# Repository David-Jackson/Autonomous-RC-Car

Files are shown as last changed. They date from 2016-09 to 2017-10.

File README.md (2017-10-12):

# Autonomous RC Car
###### David Jackson - Summer 2016

## Objective

Develop an autonomous remote-controlled (RC) car using an Arduino and PID controllers.

## Introduction

The idea of developing an autonomous RC car was brought up by [Dr. Peters](http://dianelpeters.com/) and initially developed by Dwarkesh Iyengar in October of 2015 [(link)](http://dianelpeters.com/DSCC_2015_Development_of_a_Miniaturized_Autonomous_Vehicle.pdf). Iyengar used a microcontroller unit to control the car. The microcontroller would receive commands and transmit data to a myRIO controller unit using Xbee radio transmitters. Building on Iyengar’s work, the goal of this project was to place the controller in the RC car, removing the dependency on the myRIO controller and making the car fully autonomous.

## Iterations

This project went through three design iterations during the author’s term.

### Iteration 1: Servo Mounted LIDAR

The first design iteration centered around using one LIDAR sensor  mounted to a servo motor to measure the distance to the vehicle’s surroundings. The servo motor would rotate 90 degrees, obtaining a distance reading at every degree interval. Wiring for the Lidar/Servo assembly and the Arduino can be seen in [Figure 1](#fig-1). This concept was first tested by placing the LIDAR/Servo assembly in 12 inches away from a wall. The servo motor looped through 45 and 135 degrees and back with different delay times between degrees ranging from 5 and 50 milliseconds. This was repeated 10 times for data validation. 

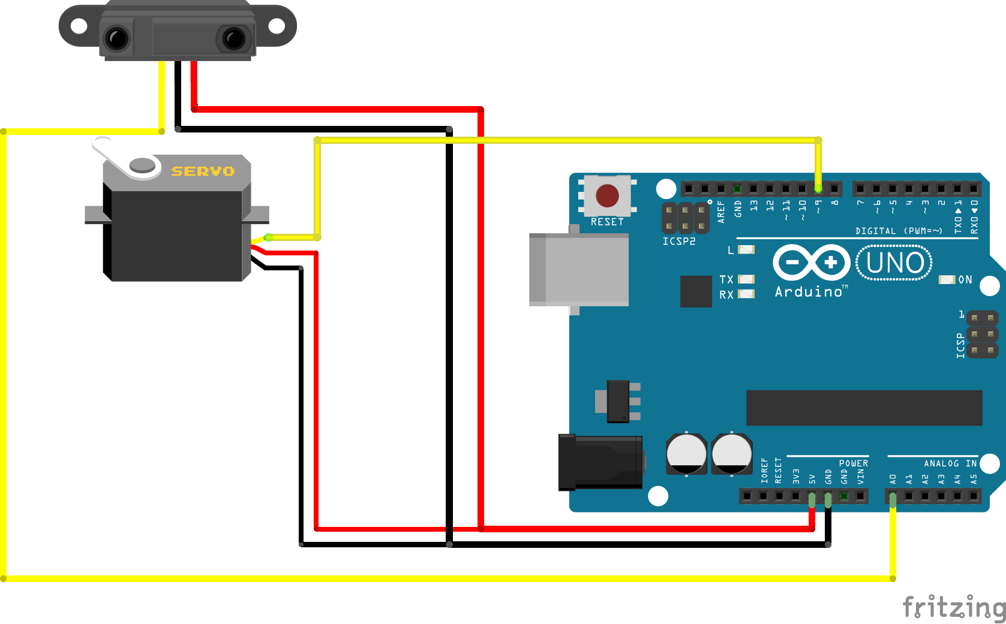
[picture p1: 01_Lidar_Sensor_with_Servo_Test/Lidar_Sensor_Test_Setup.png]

Figure 1: LIDAR/Servo Wiring Schematic

The results of the LIDAR/Servo test showed a deviation of around 10 cm between measurements at all speeds tested. This result was not within the accuracy needed for this project. A closer look into the specification sheet for the sensor showed a range between 0 and 40 meters and an accuracy of 0.025 meters. The LIDAR sensor was meant for larger-scale use where the difference between centimeters was not as important. IR distance sensors were implemented as an alternative to LIDAR, which is described in Iteration 3.

### Iteration 2: Radio Transmission Data Collection

In an attempt to collect real-time analytics from the RC car without the need of a wire, two radio transmitters  where considered. Wiring schematic for this iteration can be seen in [Figure 2](#fig-2). An Arduino Nano was used as the controller. The controller was connected to an accelerometer/gyroscope/ magnetometer board  for acceleration readings and the steering potentiometer for steering direction readings. Additionally, the controller was connected to a bi-directional motor controller IC, also called a H-bridge to control the speed and direction of the steering and drive motors (in Iteration 3 this was replaced with the Adafruit Motor Shield, which is based on a similar chip). Finally, he controller was then connected to the radio transmitter, which would send acceleration, steering direction, and motor speed data to the radio receiver, seen in [Figure 3](#fig-3), which would then be able to be seen on a computer. 

During testing, the Arduino controller took approximately 1.5 seconds to collect and send the data to the radio receiver. This delay was most likely due to the lack of processing power on the Arduino and could be avoided with a more powerful controller. This large of a delay in sensor data acquisition would be detrimental to the performance of the controller, so the concept of relaying data using radio was tabled and another iteration was developed.

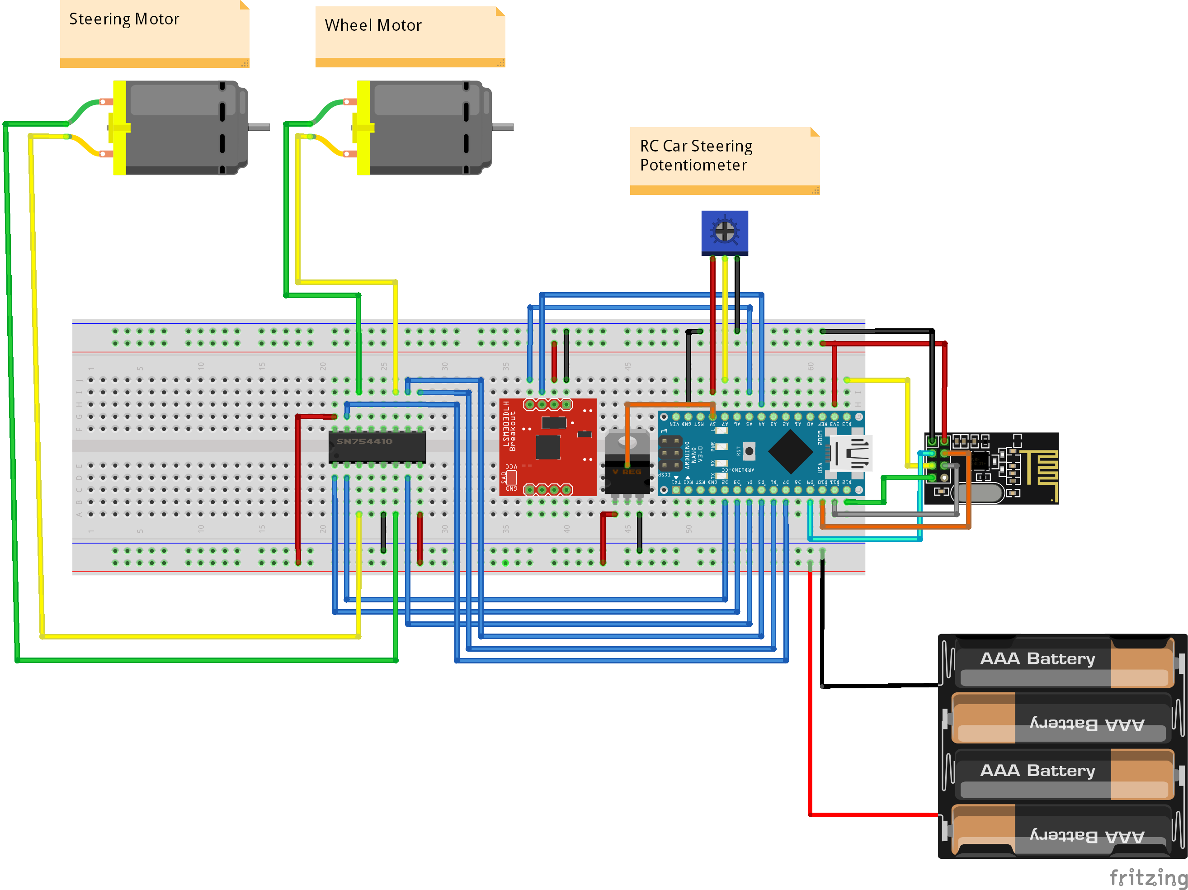
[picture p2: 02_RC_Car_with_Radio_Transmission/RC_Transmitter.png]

Figure 2: Radio Transmitter Controller Wiring Schematic

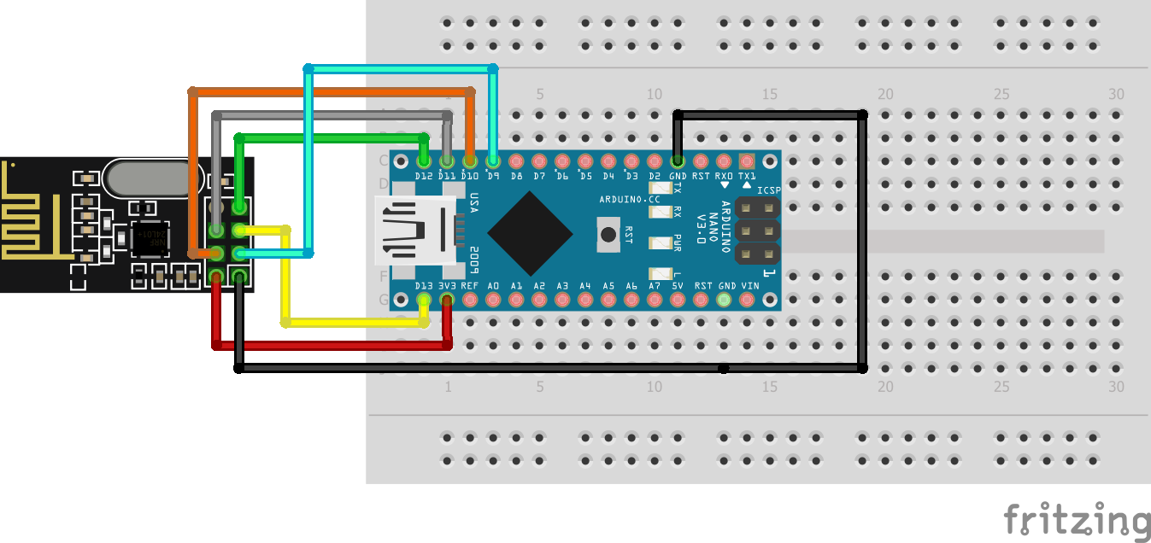
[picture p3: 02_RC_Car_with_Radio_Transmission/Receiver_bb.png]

Figure 3: Radio Receiver Module

### Iteration 3: RC Car with IR Distance Sensors

The final design of the autonomous RC car consisted of three [IR distance sensors](https://www.amazon.com/GP2Y0A21YK0F-Sharp-Distance-10-80cm-Compatible/dp/B00IMOSEJA), an Arduino, and two PID controllers. The wiring schematic for this design can be found in [Figure 4](#fig-4). This iteration was completely self-sufficient and did not require any radio transmission or outside control. Adapted from Microsoft’s Internet of Things [Github repository](https://github.com/ms-iot/wod-autorc)  on an autonomous RC car, the vehicle would determine its surroundings using the IR sensors and decide whether to turn, stop, or continue straight. 

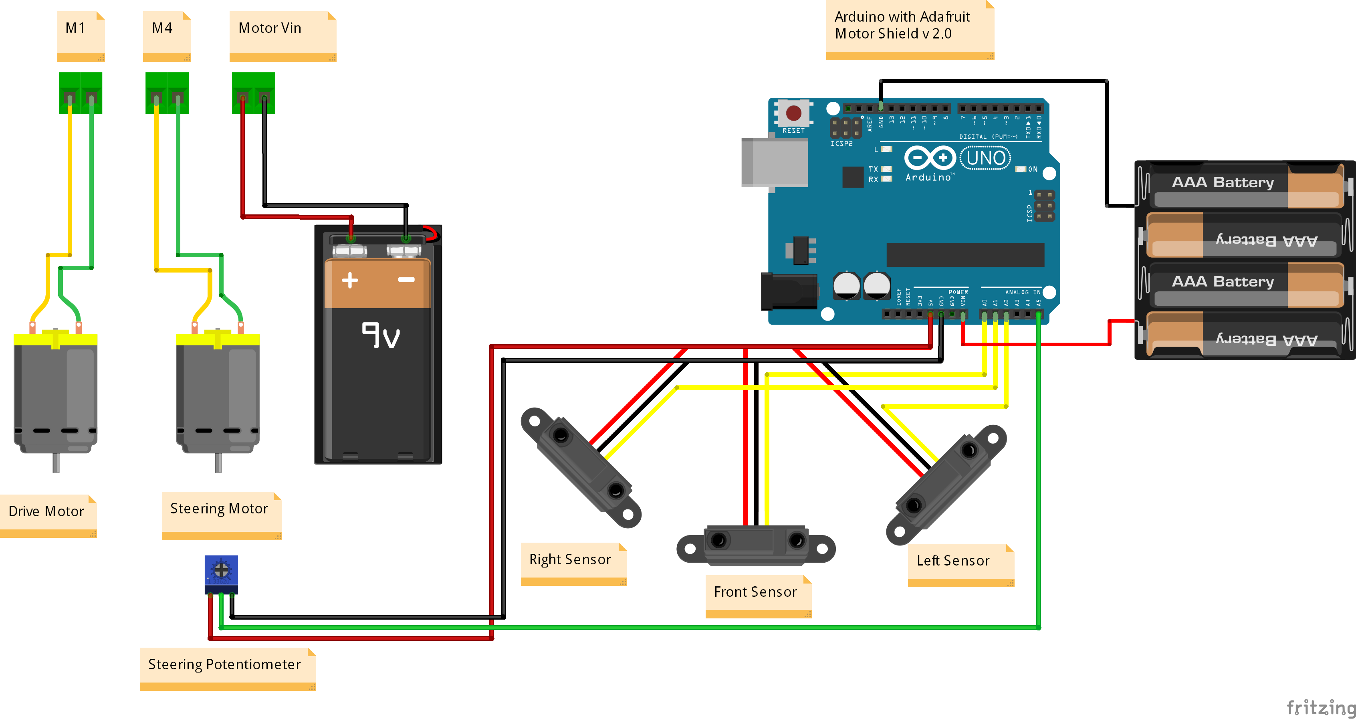
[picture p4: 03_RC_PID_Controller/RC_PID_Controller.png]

Figure 4: RC Car with IR Distance Sensors Wiring Diagram 

This design was similar to the radio transmitter iteration, except with an Arduino Uno instead of an Arduino Nano, an Adafruit Motor Shield v2.0 instead of the H-bridge Motor Driver IC, and with the addition of three IR distance sensors mounted to the front of the vehicle to measure direction straight ahead, to the right of the vehicle, and to the left of the vehicle. M1, M4, and Motor Vin seen in [Figure 4](#fig-4) represent the terminal blocks on the motor shield. It is also important to notice that the Arduino and motors are being powered by two different power sources to eliminate sensor noise produced by the motors’ energy consumption. 

#### Arduino PID Code

Below is all the code relating to the Arduino PID controller library. For a complete code file, see the code in the [project folder](/03_RC_PID_Controller/Arduino Code/IS_controller_2/IS_controller_2.ino).

Include the Arduino PID Library.
```c++
#include<PID_v1.h>
```

Next, define the variables used for the Drive PID Controller.
```c++
float Kp_drive = 0.8;  // Proportional Gain
float Ki_drive = 0.07; // Integral Gain
float Kd_drive = 0.12; // Derivative Gain
double Setpoint_drive, Input_drive, Output_drive;                                       
```

Initilize the Drive PID Controller.
```c++
PID drivePID(&Input_drive, &Output_drive, &Setpoint_drive, Kp_drive, Ki_drive, Kd_drive, DIRECT);
```

Define Variables for the Steering PID Controller.
```c++
float Kp_steer = 0.8;
float Ki_steer = 0.07;
float Kd_steer = 0.12; 
double Setpoint_steer, Input_steer, Output_steer;                                       
```

Initilize the Steering PID Controller.
```c++
PID steerPID(&Input_steer, &Output_steer, &Setpoint_steer, Kp_steer, Ki_steer, Kd_steer, DIRECT);
```

In the setup() function, set the Drive PID setpoint, the PID mode, and the output limits. In this case the output is going to be the speed of the motor, which we want to be between -50 (reverse) and 50 (forward). NOTE: the maximum motor speed is -255 and 255. 
```c++
Input_drive = readPosition();
Setpoint_drive = 300;
drivePID.SetMode(AUTOMATIC);
drivePID.SetOutputLimits(-50, 50);
```

Now do the same for the Steering PID controller, with the motor speed being limited to between -40 and 40.
```c++
Input_steer = readPosition();
Setpoint_steer = 650;
steerPID.SetMode(AUTOMATIC);
steerPID.SetOutputLimits(-40, 40);
```

In the loop() function, read angle of the steering wheels from the potentiometer, compute the PID response, and set the motor speed accordingly.
```c++
Input_steer = readSteering();
steerPID.Compute();
setSteerSpeed(Output_steer);
```

Read angle of the steering wheels from the middle IR distance sensor, compute the PID response, and set the motor speed accordingly. 
```c++
Setpoint_drive = 300;
Input_drive = readPosition();
drivePID.Compute();
if (stopped) {
  setDriveSpeed(0);
} else {
  setDriveSpeed(Output_drive);
}
```

## Conclusions

This independent study was able to design and create an autonomous RC car using an Arduino. The Arduino uses IR distance sensors to determine its surroundings and a potentiometer to determine the angle of the front wheels. The Arduino PID library was successfully implemented on the Arduino using two controllers: one for the control of the angle of the front wheels, and one for the speed of the driven rear wheels. 

In the continuation of this project, the author recommends fine tuning of the PID controllers and to add a data collection unit to the Arduino. The drive PID controller should be fine-tuned to an over damped controller to eliminate any overshoot when approaching an object. Additionally, fine-tuning the steering controller will also eliminate any steering overshoot and will guarantee the steering will reach steady-state. The addition of a data collection unit would be very beneficial to this project to analyze vehicle acceleration and sensor effectiveness. Data collection can be added to the Arduino using a [Data Logger shield](https://www.amazon.com/SD-Shield-for-Arduino-v4-0/dp/B00BPGPNH8) or even an [Ethernet Shield](https://www.amazon.com/Ethernet-Shield-Network-Expansion-Arduino/dp/B00AXVX5D0/), which both include the ability to read and write files to an SD card.

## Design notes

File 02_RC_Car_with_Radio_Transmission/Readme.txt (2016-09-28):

08/12/2016

The idea behind this design was to be able to transmit data wirelessly to a computer to analyse the RC Car's current state. This included the vehicle's acceleration, it's proximity to other objects, and the current motor speeds. However, due to the hardware limitations of the accelerometer and Arduino, the time in between transmissions averages 1.5 seconds. This large of a duration between transmissions would not yield usable data, so a different design was considered.

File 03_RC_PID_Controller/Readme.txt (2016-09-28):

09/07/2016

This design was inspired by Microsoft's Internet of Devices Github project. It involves infrared distance sensors and PID controllers to sense the vehicle's surroundings and make a decision on where to move next.

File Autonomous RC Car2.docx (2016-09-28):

# Autonomous RC Car

###### David Jackson - Summer 2016

## Objective

Develop an autonomous remote-controlled (RC) car using an Arduino and PID controllers.

## Introduction

The idea of developing an autonomous RC car was conceived by Dr. Peters and initially developed by Dwarkesh Iyengar in October of 2015 (link) (http://dianelpeters.com/DSCC_2015_Development_of_a_Miniaturized_Autonomous_Vehicle.pdf). Iyengar used a microcontroller unit to control the car. The microcontroller would receive commands and transmit data to a myRIO controller unit using Xbee radio transmitters. Building on Iyengar’s work, the goal of this project was to place the controller in the RC car, removing the dependency on the myRIO controller and making the car fully autonomous.

## Iterations

This project went through three design iterations during the author’s term.

### Iteration 1: Servo Mounted LIDAR

The first design iteration centered around using one LIDAR sensor mounted to a servo motor to measure the distance to the vehicle’s surroundings. The servo motor would rotate 90 degrees, obtaining a distance reading at every degree interval. Wiring for the Lidar/Servo assembly and the Arduino can be seen in Figure 1. This concept was first tested by placing the LIDAR/Servo assembly in 12 inches away from a wall. The servo motor looped through 45 and 135 degrees and back with different delay times between degrees ranging from 5 and 50 milliseconds. This was repeated 10 times for data validation.

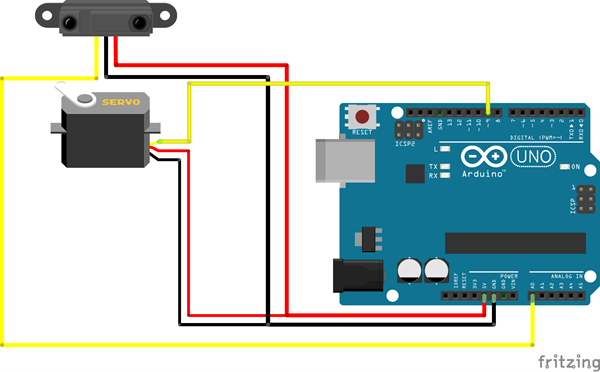
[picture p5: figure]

Figure 1: LIDAR/Servo Wiring Schematic

The results of the LIDAR/Servo test showed a deviation of around 10 cm between measurements at all speeds tested. This result was not within the accuracy needed for this project. A closer look into the specification sheet for the sensor showed a range between 0 and 40 meters and an accuracy of 0.025 meters. The LIDAR sensor was meant for larger-scale use where the difference between centimeters was not as important. IR distance sensors were implemented as an alternative to LIDAR, which is described in Iteration 3.

### Iteration 2: Radio Transmission Data Collection

In an attempt to collect real-time analytics from the RC car without the need of a wire, two radio transmitters where considered. Wiring schematic for this iteration can be seen in Figure 2 (https://jbt.github.io/markdown-editor/). An Arduino Nano was used as the controller. The controller was connected to an accelerometer/gyroscope/ magnetometer board for acceleration readings and the steering potentiometer for steering direction readings. Additionally, the controller was connected to a bi-directional motor controller IC, also called a H-bridge to control the speed and direction of the steering and drive motors (in Iteration 3 this was replaced with the Adafruit Motor Shield, which is based on a similar chip). Finally, he controller was then connected to the radio transmitter, which would send acceleration, steering direction, and motor speed data to the radio receiver, seen in Figure 3, which would then be able to be seen on a computer.

During testing, the Arduino controller took approximately 1.5 seconds to collect and send the data to the radio receiver. This delay was most likely due to the lack of processing power on the Arduino and could be avoided with a more powerful controller. This large of a delay in sensor data acquisition would be detrimental to the performance of the controller, so the concept of relaying data using radio was tabled and another iteration was developed.

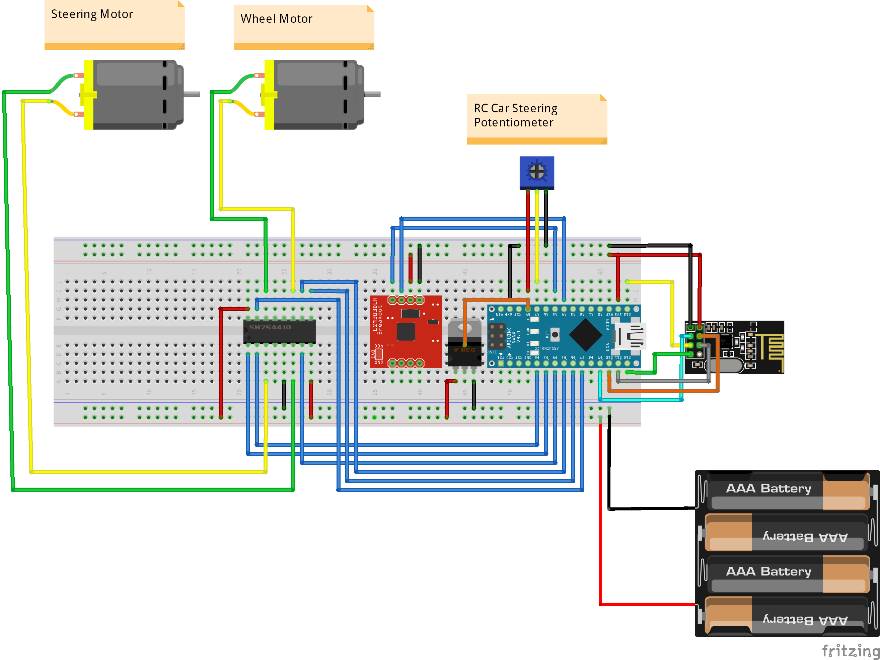
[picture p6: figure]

Figure 2: Radio Transmitter Controller Wiring Schematic


Figure 3: Radio Receiver Module

### Iteration 3: RC Car with IR Distance Sensors

The final design of the autonomous RC car consisted of three IR distance sensors (https://www.amazon.com/GP2Y0A21YK0F-Sharp-Distance-10-80cm-Compatible/dp/B00IMOSEJA), an Arduino, and two PID controllers. The wiring schematic for this design can be found in Figure 4. This iteration was completely self-sufficient and did not require any radio transmission or outside control. Adapted from Microsoft’s Internet of Things Github repository (https://github.com/ms-iot/wod-autorc) on an autonomous RC car, the vehicle would determine its surroundings using the IR sensors and decide whether to turn, stop, or continue straight.

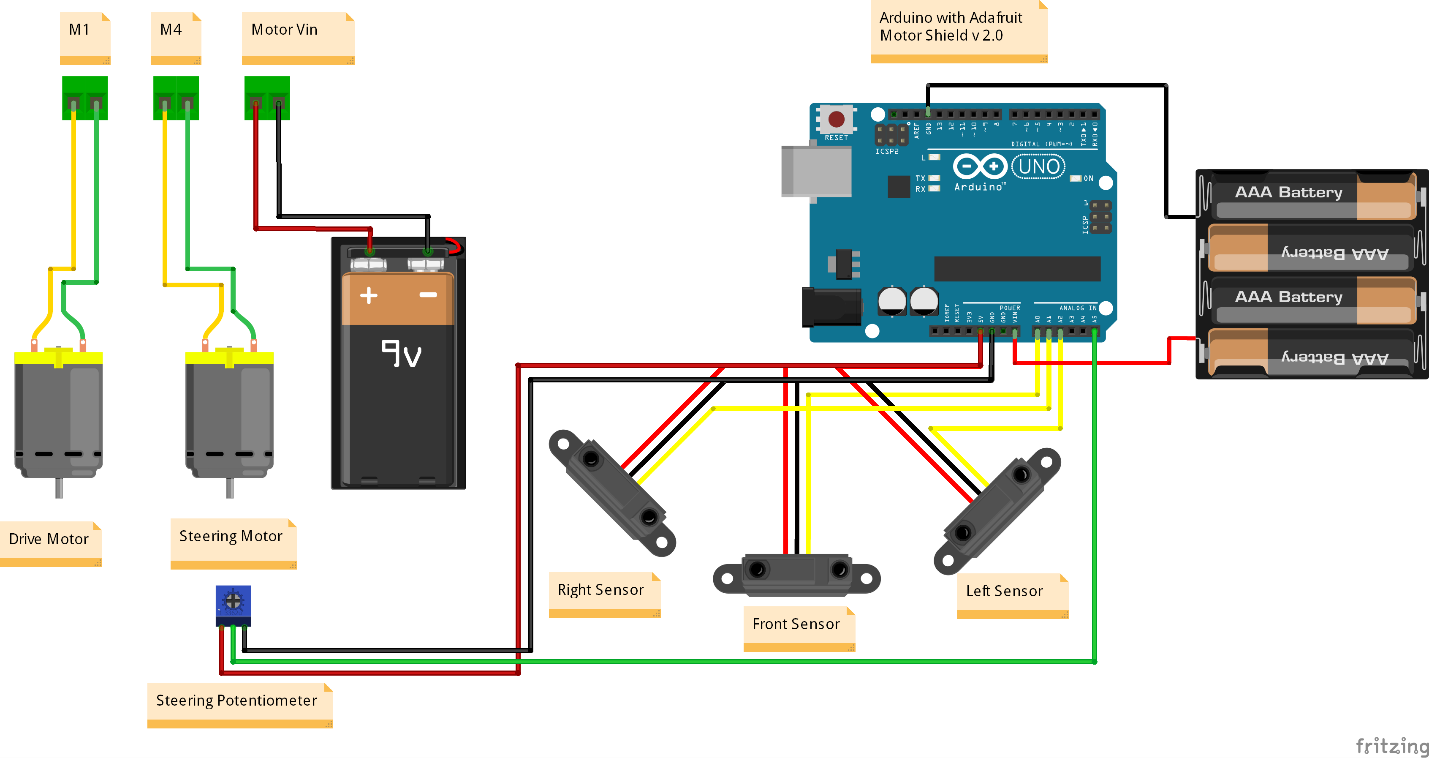
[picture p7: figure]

Figure 4: RC Car with IR Distance Sensors Wiring Diagram

This design was similar to the radio transmitter iteration, except with an Arduino Uno instead of an Arduino Nano, an Adafruit Motor Shield v2.0 instead of the H-bridge Motor Driver IC, and with the addition of three IR distance sensors mounted to the front of the vehicle to measure direction straight ahead, to the right of the vehicle, and to the left of the vehicle. M1, M4, and Motor Vin seen in Figure 4 represent the terminal blocks on the motor shield. It is also important to notice that the Arduino and motors are being powered by two different power sources to eliminate sensor noise produced by the motors’ energy consumption.

#### Arduino PID Code

Below is all the code relating to the Arduino PID controller library. For a complete code file, see the code in the project folder.

Include the Arduino PID Library.

#include<PID_v1.h>

Next, define the variables used for the Drive PID Controller.

float Kp_drive = 0.8; // Proportional Gain

float Ki_drive = 0.07; // Integral Gain

float Kd_drive = 0.12; // Derivative Gain

double Setpoint_drive, Input_drive, Output_drive;

Initilize the Drive PID Controller.

PID drivePID(&Input_drive, &Output_drive, &Setpoint_drive, Kp_drive, Ki_drive, Kd_drive, DIRECT);

Define Variables for the Steering PID Controller.

float Kp_steer = 0.8;

float Ki_steer = 0.07;

float Kd_steer = 0.12;

double Setpoint_steer, Input_steer, Output_steer;

Initilize the Steering PID Controller.

PID steerPID(&Input_steer, &Output_steer, &Setpoint_steer, Kp_steer, Ki_steer, Kd_steer, DIRECT);

In the setup() function, set the Drive PID setpoint, the PID mode, and the output limits. In this case the output is going to be the speed of the motor, which we want to be between -50 (reverse) and 50 (forward). NOTE: the maximum motor speed is -255 and 255.

Input_drive = readPosition();

Setpoint_drive = 300;

drivePID.SetMode(AUTOMATIC);

drivePID.SetOutputLimits(-50, 50);

Now do the same for the Steering PID controller, with the motor speed being limited to between -40 and 40.

Input_steer = readPosition();

Setpoint_steer = 650;

steerPID.SetMode(AUTOMATIC);

steerPID.SetOutputLimits(-40, 40);

In the loop() function, read angle of the steering wheels from the potentiometer, compute the PID response, and set the motor speed accordingly.

Input_steer = readSteering();

steerPID.Compute();

setSteerSpeed(Output_steer);

Read angle of the steering wheels from the middle IR distance sensor, compute the PID response, and set the motor speed accordingly.

Setpoint_drive = 300;

Input_drive = readPosition();

drivePID.Compute();

if (stopped) {

setDriveSpeed(0);

} else {

setDriveSpeed(Output_drive);

}

## Conclusions

This independent study was able to design and create an autonomous RC car using an Arduino. The Arduino uses IR distance sensors to determine its surroundings and a potentiometer to determine the angle of the front wheels. The Arduino PID library was successfully implemented on the Arduino using two controllers: one for the control of the angle of the front wheels, and one for the speed of the driven rear wheels. In the continuation of this project, the author recommends fine tuning of the PID controllers and to add a data collection unit to the Arduino. The drive PID controller should be fine-tuned to an over damped controller to eliminate any overshoot when approaching an object. Additionally, fine-tuning the steering controller will also eliminate any steering overshoot and will guarantee the steering will reach steady-state. The addition of a data collection unit would be very beneficial to this project to analyze vehicle acceleration and sensor effectiveness. Data collection can be added to the Arduino using a Data Logger shield (https://www.amazon.com/SD-Shield-for-Arduino-v4-0/dp/B00BPGPNH8) or even an Ethernet Shield (https://www.amazon.com/Ethernet-Shield-Network-Expansion-Arduino/dp/B00AXVX5D0/), which both include the ability to read and write files to an SD card.

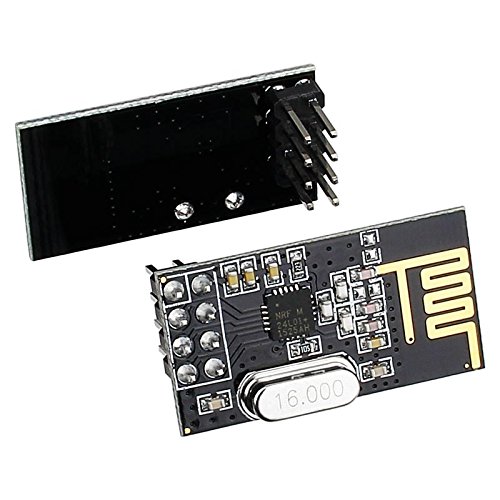
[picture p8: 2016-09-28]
02_RC_Car_with_Radio_Transmission/nRF24L01+.jpg

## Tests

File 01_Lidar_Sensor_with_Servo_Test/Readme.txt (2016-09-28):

07/29/2016

This test was meant to evaluate the possibility of using one LIDAR sensor rotating on a servo mount to sense objects in the RC Car's proximity. It was determined that the LIDAR sensor on a servo motor was not accurate enough for the purposes of this project. The sensor had too much noise and was not accurate within 5 inches.

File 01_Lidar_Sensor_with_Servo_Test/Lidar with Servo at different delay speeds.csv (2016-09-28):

Delay Between Angles (Millis) | Angle (Deg) | Distance (cm)
50 | 45 | 33
50 | 46 | 43
50 | 47 | 43
50 | 48 | 45
50 | 49 | 50
50 | 50 | 63
50 | 51 | 48
50 | 52 | 46
50 | 53 | 47
50 | 54 | 47
50 | 55 | 47
50 | 56 | 45
50 | 57 | 46
50 | 58 | 43
50 | 59 | 42
50 | 60 | 42
50 | 61 | 40
50 | 62 | 38
50 | 63 | 37
50 | 64 | 35
50 | 65 | 38
50 | 66 | 36
50 | 67 | 37
50 | 68 | 36
50 | 69 | 35
50 | 70 | 33
50 | 71 | 36
50 | 72 | 32
50 | 73 | 34
50 | 74 | 33
50 | 75 | 33
50 | 76 | 33
50 | 77 | 36
50 | 78 | 35
50 | 79 | 34
50 | 80 | 36
50 | 81 | 36
50 | 82 | 34
50 | 83 | 35
50 | 84 | 38
50 | 85 | 34
50 | 86 | 35
50 | 87 | 44
50 | 88 | 33
50 | 89 | 36
50 | 90 | 42
50 | 91 | 35
50 | 92 | 35
50 | 93 | 33
50 | 94 | 35
50 | 95 | 36
50 | 96 | 35
50 | 97 | 34
50 | 98 | 34
50 | 99 | 35
50 | 100 | 35
50 | 101 | 33
50 | 102 | 34
50 | 103 | 34
50 | 104 | 31
50 | 105 | 34
50 | 106 | 33
50 | 107 | 31
50 | 108 | 33
50 | 109 | 35
50 | 110 | 33
50 | 111 | 35
50 | 112 | 33
50 | 113 | 34
50 | 114 | 33
50 | 115 | 34
50 | 116 | 34
50 | 117 | 33
50 | 118 | 45
50 | 119 | 35
50 | 120 | 38
50 | 121 | 38
50 | 122 | 39
50 | 123 | 42
50 | 124 | 47
50 | 125 | 42
50 | 126 | 43
50 | 127 | 45
50 | 128 | 43
50 | 129 | 56
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

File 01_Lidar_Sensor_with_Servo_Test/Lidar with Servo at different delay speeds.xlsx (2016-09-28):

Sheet: All Speeds
Delay Between Angles (Millis) | Angle (Deg) | Distance (cm)
50 | 45 | 33
50 | 46 | 43
50 | 47 | 43
50 | 48 | 45
50 | 49 | 50
50 | 50 | 63
50 | 51 | 48
50 | 52 | 46
50 | 53 | 47
50 | 54 | 47
50 | 55 | 47
50 | 56 | 45
50 | 57 | 46
50 | 58 | 43
50 | 59 | 42
50 | 60 | 42
50 | 61 | 40
50 | 62 | 38
50 | 63 | 37
50 | 64 | 35
50 | 65 | 38
50 | 66 | 36
50 | 67 | 37
50 | 68 | 36
50 | 69 | 35
50 | 70 | 33
50 | 71 | 36
50 | 72 | 32
50 | 73 | 34
50 | 74 | 33
50 | 75 | 33
50 | 76 | 33
50 | 77 | 36
50 | 78 | 35
50 | 79 | 34
50 | 80 | 36
50 | 81 | 36
50 | 82 | 34
50 | 83 | 35
50 | 84 | 38
50 | 85 | 34
50 | 86 | 35
50 | 87 | 44
50 | 88 | 33
50 | 89 | 36
50 | 90 | 42
50 | 91 | 35
50 | 92 | 35
50 | 93 | 33
50 | 94 | 35
50 | 95 | 36
50 | 96 | 35
50 | 97 | 34
50 | 98 | 34
50 | 99 | 35
50 | 100 | 35
50 | 101 | 33
50 | 102 | 34
50 | 103 | 34
50 | 104 | 31
50 | 105 | 34
50 | 106 | 33
50 | 107 | 31
50 | 108 | 33
50 | 109 | 35
50 | 110 | 33
50 | 111 | 35
50 | 112 | 33
50 | 113 | 34
50 | 114 | 33
50 | 115 | 34
50 | 116 | 34
50 | 117 | 33
50 | 118 | 45
50 | 119 | 35
50 | 120 | 38
50 | 121 | 38
50 | 122 | 39
50 | 123 | 42
50 | 124 | 47
50 | 125 | 42
50 | 126 | 43
50 | 127 | 45
50 | 128 | 43
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

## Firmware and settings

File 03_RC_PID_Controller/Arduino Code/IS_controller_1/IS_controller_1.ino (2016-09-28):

#include<Servo.h>
#include<PID_v1.h>
#include "Motor.h"
#include<NewPing.h>

#define TRIGGER_PIN  5                                                //Trigger Pin for UltraSonic Sensor
#define ECHO_PIN 6                                                    //Echo Pin for UltraSonic Sensor
#define MAX_DISTANCE 30                                               //Max Distance to be sensed (cm)
const int servoPin = 9;                                               //Servo Pin
int potPin = A0;                                                      //Analog Potentiometer Pin 


float Kp = 0.8;                                                       //Initial Proportional Gain
float Ki = 0.07;                                                      //Initial Integral Gain
float Kd = 0.12;                                                      //Intitial Derivative Gain
double Setpoint, Input, Output;                                       

NewPing sonar(TRIGGER_PIN, ECHO_PIN, MAX_DISTANCE);                  //Initialize NewPing object, which is in the class 
                                                                     //  NewPing that calcualtes and digitally filters 
                                                                     //  Ultrasonic Sensor data

PID myPID(&Input, &Output, &Setpoint, Kp, Ki, Kd, DIRECT);           //Initialize PID object, which is in the class PID.
                                                                     //  This class 'filters' the error signal based on 
                                                                     //  where the Setpoint and Input is. The Output is
                                                                     //  sent to the Servo in terms of degrees.
                                                                     
Servo myServo;                                                       //Initial Servo.

Motor drive;

void setup() {

  Serial.begin(9600);                                                //Begin Serial (to show readings)
  drive.init(3, 2, 4);

  Input = readPosition();                                            //Calls function readPosition() and sets the balls
                                                                     //  position as the input to the PID algorithm
                                                                     
  Setpoint = 300;                                                    //Desired location of ball in terms of potentiometer redading
  myPID.SetMode(AUTOMATIC);                                          //Set PID object myPID to AUTOMATIC (see playground for more details)
  myPID.SetOutputLimits(-150, 150);                                    //Set Output limits to 80 and 100 degrees. This keeps my servo from 
                                                                     //  going too far each way and messing up the plant.
}

void loop()
{
 
  Setpoint = 300;                                                    //Setpoint same as above in function setup() (see above for more details)
  Input = readPosition();                                            //Input same as above in function setup() (see above for more details)
  myPID.Compute();                                                   //The 'magic' happens and algorithm computes Output in range of 80 to 100 degrees
  drive.setMotor(Output);
  
  printData(Setpoint, Input, Output);                                //Calls function printData(). Prints Setpoint, Input, and Output to Serial    
  newGains();                                                        //Calls function newGains(). Changes Kp, Ki, and Kd and prints to Serial
}

//**********************************************************************************************************************************************************
//PrintData() prints Setpoint, Input, and Output to Serial each time PID loop runs. This may cause PID loop to run a tad slower than wanted
//            so it may be helpful to use this only when testing
//**********************************************************************************************************************************************************
void printData(float set, float in, float out) {
  Serial.print("Setpoint = "); 
  Serial.print(set); 
  Serial.print(" Input = "); 
  Serial.print(in); 
  Serial.print(" Output = "); 
  Serial.print(out); 
  Serial.print("\n");
}

//**********************************************************************************************************************************************************
//newGains() watis to see if anything is typed in serial port. If there is, the values are put into Kp, Ki, and Kd. Then the values are printed to Serial.
//**********************************************************************************************************************************************************
void newGains() {
  if (Serial.available() > 0) {                                        //If there is any data in serial input, then it starts reading.
     delay(100);                                                       //Pause for a tenth of a second to readjust plant or anything else you need to do.
                                                                       //  Can be as long as needed.     
     for (int i = 0; i < 4; i = i + 1) {                               
       switch (i) { 
         case 0:                                                       //Reads 1st value in
           Kp = Serial.parseFloat(); 
           break; 
         case 1:                                                       //Reads 2st value in 
           Ki = Serial.parseFloat(); 
           break; 
         case 2:                                                       //Reads 3st value in
           Kd = Serial.parseFloat(); 
           break; 
         case 3:                                                       //Clears any remaining parts.
           for (int j = Serial.available(); j == 0; j = j - 1) { 
             Serial.read();  
           }        
           break; 
       }
     }
     Serial.print(" Kp, Ki, Kd = ");                                     //Prints new gain values to Serial
     Serial.print(Kp); 
     Serial.print(", "); 
     Serial.print(Ki); 
     Serial.print(", "); 
     Serial.println(Kd);  
     myPID.SetTunings(Kp, Ki, Kd);
   }
   
}

//**********************************************************************************************************************************************************
//readPosition() reads the position of the ball and returns balls position in cm. 
//**********************************************************************************************************************************************************

float readPosition() {
  return analogRead(A1);
}

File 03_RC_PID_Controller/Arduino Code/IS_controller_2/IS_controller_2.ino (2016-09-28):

// Adafruit Motor Shield Libraries
#include <Wire.h>
#include <Adafruit_MotorShield.h>
#include "utility/Adafruit_MS_PWMServoDriver.h"

// PID Library
#include<PID_v1.h>


// define IR sensor Pins
int STRAIGHT_PIN = 0; // analog pin for straight forward IR sensor
int RIGHT_PIN = 1; // analog pin for right IR sensor
int LEFT_PIN = 2; // analog pin for left IR sensor

// define constants
int TURN_THRESHOLD = 600; // side sensor reading when car will turn
boolean stopped = false; // variable to tell when car is stopped/should stop



// Create the motor shield object with the default I2C address
Adafruit_MotorShield AFMS = Adafruit_MotorShield();

// Select which 'port' M1, M2, M3 or M4. In this case, M1 is the drive and M4 is the steering
Adafruit_DCMotor *drive = AFMS.getMotor(1);
Adafruit_DCMotor *steer = AFMS.getMotor(4);

float Kp_drive = 0.8;                                                       //Initial Proportional Gain
float Ki_drive = 0.07;                                                      //Initial Integral Gain
float Kd_drive = 0.12;                                                      //Intitial Derivative Gain
double Setpoint_drive, Input_drive, Output_drive;                                       

PID drivePID(&Input_drive, &Output_drive, &Setpoint_drive, Kp_drive, Ki_drive, Kd_drive, DIRECT);


float Kp_steer = 0.8;
float Ki_steer = 0.07;
float Kd_steer = 0.12; 
double Setpoint_steer, Input_steer, Output_steer;                                       


PID steerPID(&Input_steer, &Output_steer, &Setpoint_steer, Kp_steer, Ki_steer, Kd_steer, DIRECT);


void setup() {

  Serial.begin(9600);

  
  AFMS.begin();  // create with the default frequency 1.6KHz
  // Set drive speed to start, from 0 (off) to 255 (max speed)
  drive->setSpeed(0);
  drive->run(FORWARD);
  // turn on motor
  drive->run(RELEASE);
  // Set steer speed to start, from 0 (off) to 255 (max speed)
  steer->setSpeed(0);
  steer->run(FORWARD);
  // turn on motor
  steer->run(RELEASE);

  
  Input_drive = readPosition();
  Setpoint_drive = 300;
  drivePID.SetMode(AUTOMATIC);
  drivePID.SetOutputLimits(-50, 50);


  Input_steer = readPosition();
  Setpoint_steer = 650;
  steerPID.SetMode(AUTOMATIC);
  steerPID.SetOutputLimits(-40, 40);
  
}

long prevMillis = 0;

void loop()
{

  
  float right = readRight();
  float left = readLeft();
  stopped = false;
  
  if (right > TURN_THRESHOLD && left > TURN_THRESHOLD) {
    // stop
    Serial.print("STOPPED");
    stopped = true;
  } else if (right > TURN_THRESHOLD) {
    // turn left
    Serial.print("Left");
    Setpoint_steer = 500;
  } else if (left > TURN_THRESHOLD) {
    // turn right
    Serial.print("right");
    Setpoint_steer = 900;
  } else {
    Setpoint_steer = 700;
    Serial.print("straight");
  }

  Serial.print(" - ");
  Serial.println(readSteering());

  
  // calculate Steering PID Response
//  if (millis() - prevMillis > 5000) {
//    Setpoint_steer = 550;
//  }
//  if (millis() - prevMillis > 10000) {
//    prevMillis = millis();
//    Setpoint_steer = 900;
//  }
  Input_steer = readSteering();
  steerPID.Compute();
  setSteerSpeed(Output_steer);

  //printData(Setpoint_steer, Input_steer, Output_steer);
  
  // calculate Drive PID Response
  Setpoint_drive = 300;
  Input_drive = readPosition();
  drivePID.Compute();
  if (stopped) {
    setDriveSpeed(0);
  } else {
    setDriveSpeed(Output_drive);
  }
  delay(10);
}


void setDriveSpeed(int spd) {
  if (spd < 0) {
    // set to reverse
    drive->run(BACKWARD);
    drive->setSpeed(-spd);
  } else {
    // set to forward
    drive->run(FORWARD);
    drive->setSpeed(spd);
  }
}

void setSteerSpeed(int spd) {
  if (spd < 0) {
    // set to reverse
    steer->run(BACKWARD);
    steer->setSpeed(-spd);
  } else {
    // set to forward
    steer->run(FORWARD);
    steer->setSpeed(spd);
  }
}


void printData(float set, float in, float out) {
  Serial.print("Setpoint = "); 
  Serial.print(set); 
  Serial.print(" Input = "); 
  Serial.print(in); 
  Serial.print(" Output = "); 
  Serial.print(out); 
  Serial.print("\n");
}
float readPosition() {
  return analogRead(STRAIGHT_PIN);
}

float readSteering() {
  return analogRead(A5);
}

float readRight() {
  return analogRead(RIGHT_PIN);
}

float readLeft() {
  return analogRead(LEFT_PIN);
}

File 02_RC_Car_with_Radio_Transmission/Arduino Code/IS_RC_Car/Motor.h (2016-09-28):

int enablePin = 3;
int in1Pin = 2;
int in2Pin = 4;


int index = 0;
unsigned long completedTime = 0;
int instrLength = 4;
int instr[4][2] = {
  {-255, 2000},
  {0, 5000},
  {255, 2000},
  {0, 5000}
};

void check(unsigned long ms) {
  if(ms - completedTime > instr[index][1]) {
    completedTime += instr[index][1];
    index = (index + 1) % instrLength;
  }
  //setMotor(instr[index][0]);
}

void setMotor(int spd) {
  boolean rev = spd >= 0;
  analogWrite(enablePin, abs(spd));
  digitalWrite(in1Pin, !rev);
  digitalWrite(in2Pin, rev);
}

void Motor_Setup() {
  pinMode(enablePin, OUTPUT);
  pinMode(in1Pin, OUTPUT);
  pinMode(in2Pin, OUTPUT);
}

void Motor_Loop() {
  check(millis());
}
